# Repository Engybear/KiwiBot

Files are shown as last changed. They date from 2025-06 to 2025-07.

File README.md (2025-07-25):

# KiwiBot
<div align = "center"> 
  
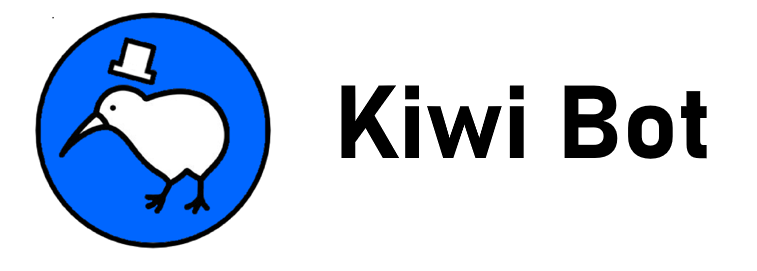
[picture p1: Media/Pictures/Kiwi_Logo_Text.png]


</div>

<!-- TOC -->
* [KiwiBot](#kiwibot)
  * [Inspiration, Purpose and Goals](#inspiration-purpose-and-goals)
  * [What It Does / Overview](#what-it-does--overview)
  * [File Organization / How It's Made](#file-organization--how-its-made)
  * [Challenges Faced](#challenges-faced)
  * [Accomplishments To Be Proud Of](#accomplishments-to-be-proud-of)
  * [Next Steps](#next-steps)

## Inspiration, Purpose and Goals
The public Ontario High School Curriculum only offers 6 courses regarding Computer Engineering and 0 courses regarding Electrical Engineering. Additionally schools are NOT required to facilitate this very limited selection of courses (only 9 out of the 26 schools in the Dufferin Peel Cathloic District offer a Computer Technology course). On interviewing high school teachers, many were frustrated that students say they want to be in STEM but don't know anything about it.

This project's motivation is to bridge the gap between classroom concepts and a physical, engaging and interactive module with the goal of sparking an interest in high schoolers to pursue engineering at the high school level.

The primary design goals of this project were to do what other hobby robots didn't, to invoke a sense of technically prowress. Research identified omni-directional movement, a single-handed control system, and real-time feedback to be areas of focus.

## What It Does / Overview
KiwiBot is a small-sized (10x10x16'') robot, capable of omni-directional movement on a planar surface using a KiwiDrive drive system, controlled by a gyroscopic sensor on a one-size-fits-all wearable glove and makes use of LED states and an accompanying computer program to provide optional feedback to the user.

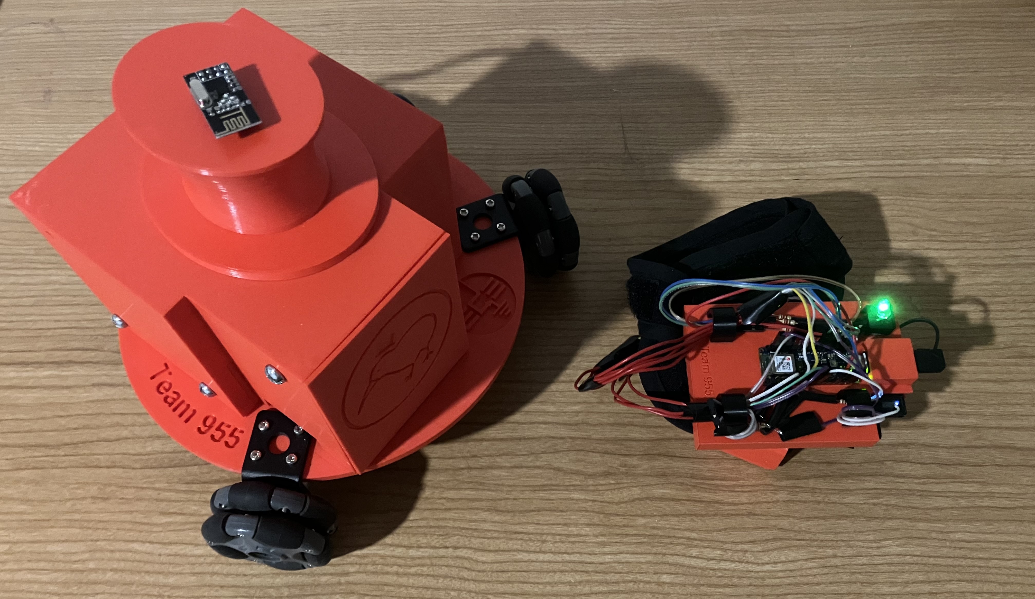
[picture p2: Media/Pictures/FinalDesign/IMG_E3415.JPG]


### Design Breakdown

Here you can see an overview of the design with inputs/outputs designated as circles at the bottom, primarily virtual processes in green, robot encapsulated structures in pink, handheld/glove controller encapsulated structures in blue, and the accompanied UI display structure in orange.

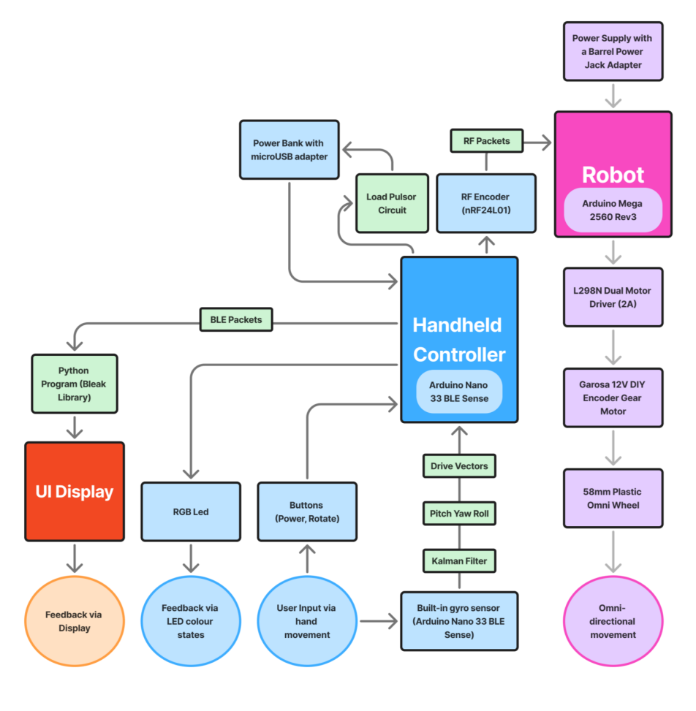
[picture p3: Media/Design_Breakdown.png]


- Refer to Media/Pictures and Videos to see KiwiBot in action

## File Organization / How It's Made

Refer to User Guide for setup and usage information

Refer to Construction Guide for system design information

Refer to arduino_sketches for the logic of the robot, the glove controller and tuning which are written in `C++`

Refer to scripts for supportive visuals that can be run on a computer which are written in `Python`

Refer to CAD_Files for CAD design and 3D printing files created in `Fusion360`

## Challenges Faced
The greatest challenge of this project was getting accurate tilt controls that felt good and intuitive. Of the ~25 people that used the design, it’s clear that for some it comes very easily,
while for others it’s hard to understand. During the early phases of construction, one of the major choices being made was to use either an MPU6050 or an MCU with built-in IMUs
like the Arduino Nano 33 BLE Sense Rev2 (BMI270 + BMM150). Due to a desire to simplify the hardware on the Controller as much as possible along with budget constraints, the Arduino Board with built-in sensors would be selected. It should be noted that both IMUs are able to achieve a IMU measurement range of +/- 4 Gs on the accelerometer and +/- 2000 deg/s on the
gyroscope, but the Arduino also has the BMM150 to make it a 9-axis sensor. Another consideration going into choosing the Arduino is that with an internal measurement unit built-in, sampling rate is automatically handled and overhead to prompt the sensors is minimized, whereas with an external measurement unit, communication would have to be over a serial bus and potentially susceptible to noise from other hardware on the controller. 

It should also be noted after much testing, that the magnetometer (BMM150) is highly unreliable and susceptible to noise in the environment, hence its influence in the Kalman Filter design was heavily reduced to be a simple error tracking term for the gyroscopic sensor’s yaw predictions. Over the course of the project several different filters would be tested to get better results. The process can be seen in the gyro_tuning.ino file, which contains the functions used to tune the gyroscopic and magnetometer sensors, as well as manually analyzing the predictions of independent sensors alone, complementary filters, and Madgwick filters. To see these, simply connect the Arduino Nano to a computer, uncomment a desired function in the main loop of the program in Arduino IDE and upload the sketch. The Kalman filter would however be selected and implementing in the gyro_main_ble.ino file because it was highly tunable to the design, leading to the best results given the condition that the Controller is not turned upside down as a result of using Euler angles over quaternions. It is a result of all these considerations and a LOT of testing and tuning for error margins that this challenge was conquered.

## Accomplishments To Be Proud Of
This project has two major accomplistments I would personally like to highlight:

I would firstly like to shoutout two private high schools, Sherwood Heights School and Kings Christian Collegiate, for allowing me to present the design in a live environment to high school students who wanted to learn more about engineering. Seeing a project through to a point were a target audience can use the design and I can collect feedback for further adjustments and improvements is always a pleasure and making an impact on worth celebrating. I should also note that on follow-up conversations with my contacts at these schools, I would learn that students would continue to discuss the event for a few days after it occured.

Secondly I'd like to shoutout my supervising professor, Belinda Wang, who nominated the project for a distinction in recognizing the effort that was put in and the results it would achieve. Additionally, the professor, among the other schools who were also interested in acquiring the project, was so impressed she would acquire KiwiBot for $591.99 to use in future demonstrations in highlighting the engineering design process.



## Next Steps
1. Single-handed tilt controls are unique and technically impressive to students, as well as
covers up the floaty control and motor drift during runtime. That said, there are ultimately
better methods of control. It was determined about halfway through the project that a
controller with 2 analog potentiometer joysticks (one to control orientation and one to
control direction of movement; or simply just one for the latter) rather than a glove would
be easier and snappier to control, assuming PID control is implemented to remove motor
drift. It is entirely possible to implement a controller that does both joystick and tilt
control and can swap between those methods of control, even while maintaining the
wearable glove concept.
2. One of the major recommendations for taking this project further is reducing costs to turn
it into a workshop kit. A drastic way to do this would be to cut out the Robot entirely.
With the hardware of the Controller alone, the project would consist of the Arduino Nano
33 BLE Sense Rev2, two push buttons, an RGB Led, and the power bank. However, even
such a large power bank used in the project is not needed and can be swapped out for AA
batteries instead, given the low power nature of the Controller. This would reduce costs
approximately to $80 per kit.
3. In tandem with Recommendation 2, without a physical Robot the simulation software
should be heavily advanced. It is possible to let students CAD out their own KiwiDrive
Robot or use a base template Robot, for which they can port into a 3D software
simulation and control the Robot through a digital landscape with the Controller. Once
they have done a software simulation test, they could try their controller out on the real
thing, with one shared physical Robot, that we’ve already made. This would be a major
undertaking potentially worth another Capstone Project.
4. Another method of reducing costs would be to not use Arduino boards that come with a
lot of extra bloat hardware but rather have a person who can design custom PCBs with
select chips, which was originally intended at the start of this project. Currently ~25% of
the project costs are from the Arduino boards. This would also help reduce space these
components require.
5. The wiring of the Controller is exposed and very vulnerable to weather conditions.
Although it wasn’t in the scope of this project, it was initially desired and is
recommended that the hardware for the Controller be contained within a protective
casing.
6. Occasionally PWM/DIR wires connecting to the Arduino Mega 2560 (on the second
layer) come loose from the L298Ns (on the base layer). Find a fix for this; currently using
electrical tape as a stand-in.
7. Fix sticky button on Controller.

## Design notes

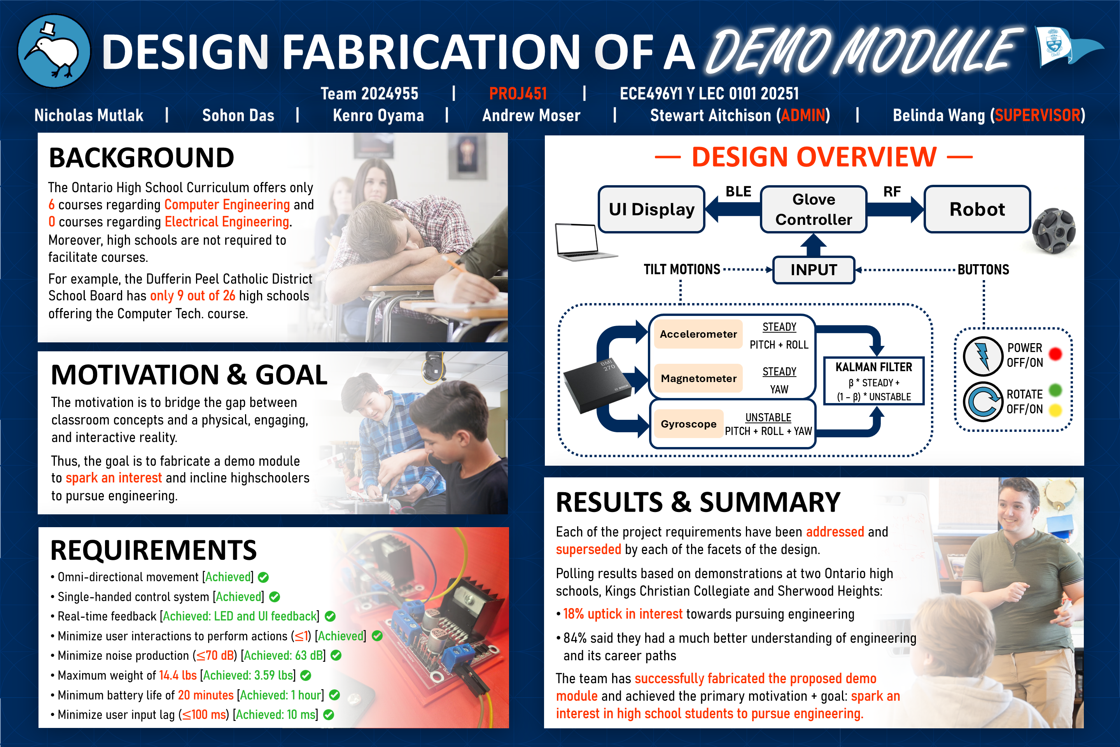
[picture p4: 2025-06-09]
Capstone_Poster.PNG

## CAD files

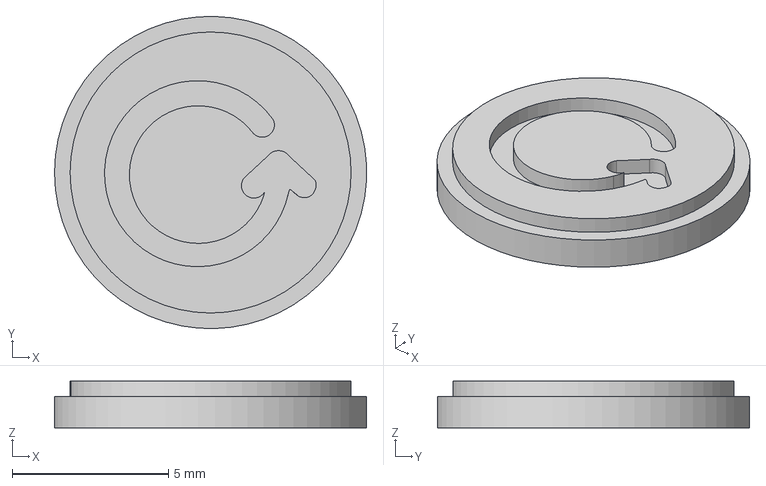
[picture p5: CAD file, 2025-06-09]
CAD_Files/glove/G2_KeyCap_Rotate.step
9.99 x 10.00 x 1.50 mm

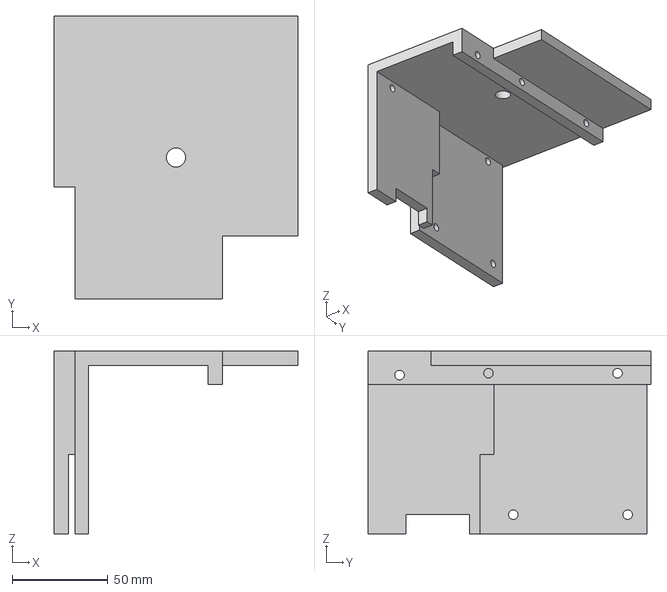
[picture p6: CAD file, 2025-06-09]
CAD_Files/robot/R2_Roof.step
127.6 x 148.0 x 95.5 mm

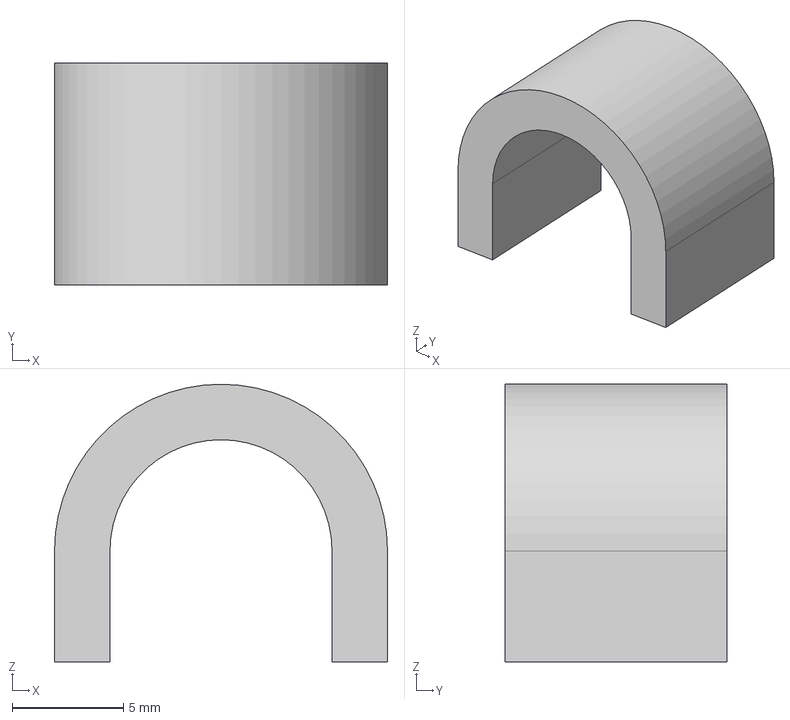
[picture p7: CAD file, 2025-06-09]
CAD_Files/glove/G2_Battery_WireHook.step
15.0 x 10.0 x 12.5 mm

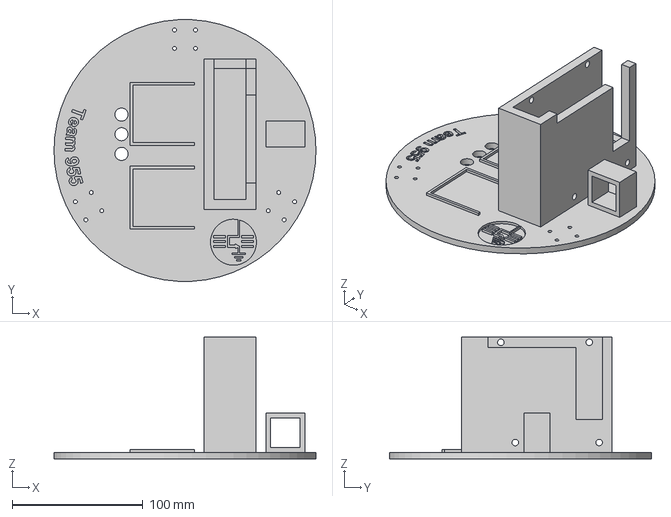
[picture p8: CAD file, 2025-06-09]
CAD_Files/robot/R2_Base.step
200.0 x 199.7 x 93.0 mm

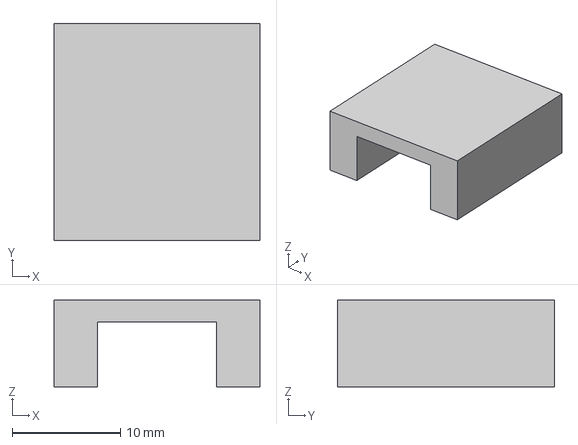
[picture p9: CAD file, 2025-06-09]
CAD_Files/glove/G2_Battery_Hook.step
19.0 x 20.0 x 8.00 mm

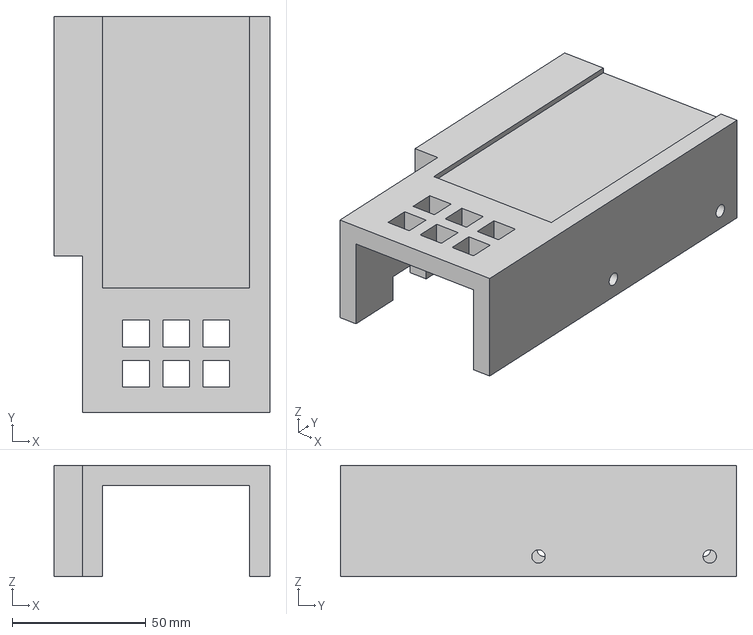
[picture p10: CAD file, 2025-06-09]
CAD_Files/robot/R2_ArduinoBase.step
80.6 x 148.0 x 41.5 mm

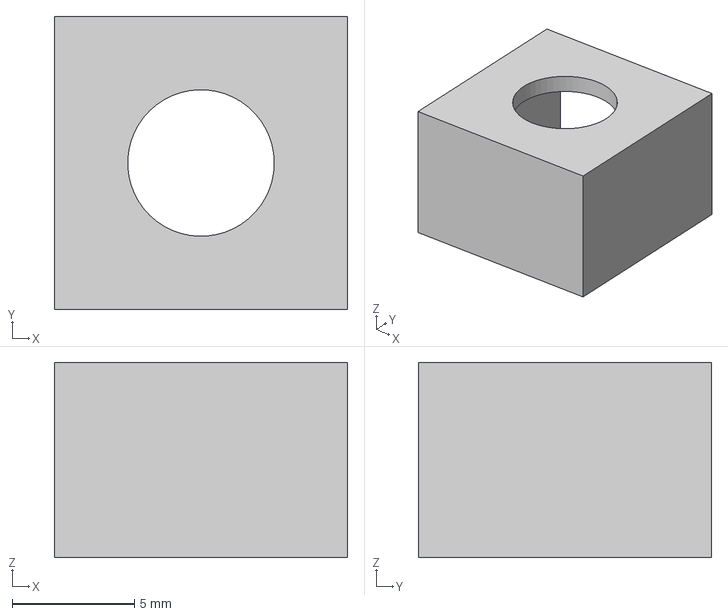
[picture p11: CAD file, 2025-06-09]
CAD_Files/glove/G2_RGB_Hook.step
12.0 x 12.0 x 8.00 mm

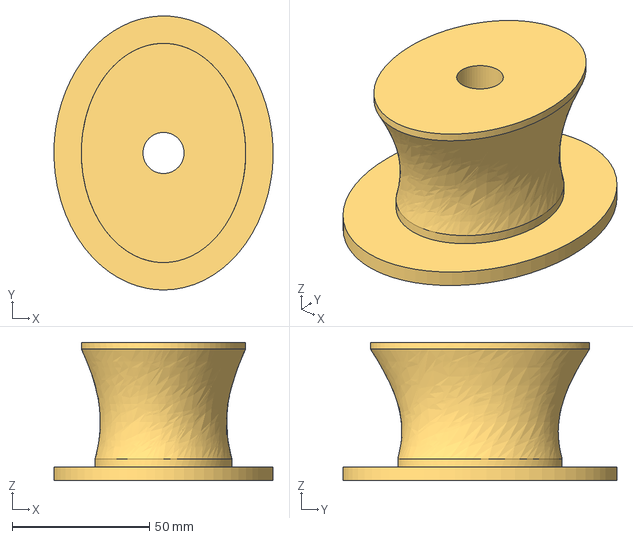
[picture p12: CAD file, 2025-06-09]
CAD_Files/robot/R2_Hat.step
79.9 x 100.0 x 50.5 mm

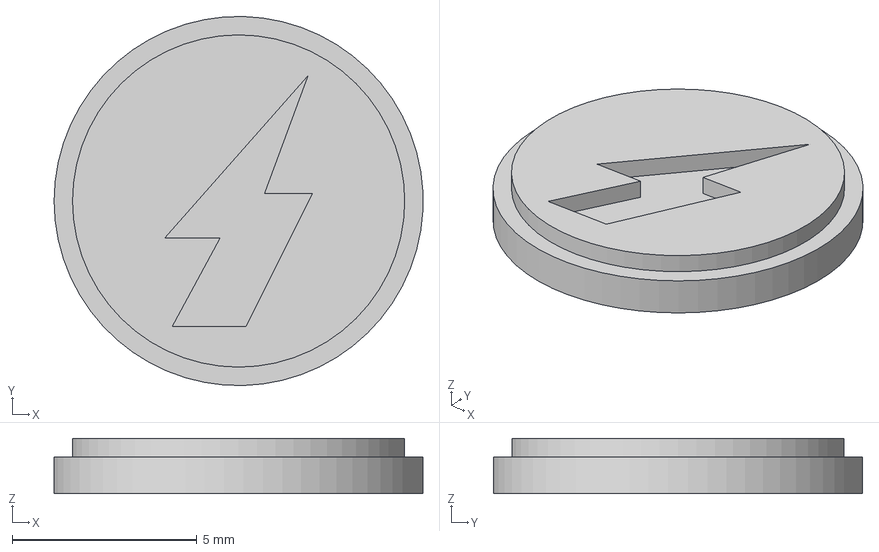
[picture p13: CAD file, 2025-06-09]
CAD_Files/glove/G2_KeyCap_Power.step
9.99 x 10.00 x 1.50 mm

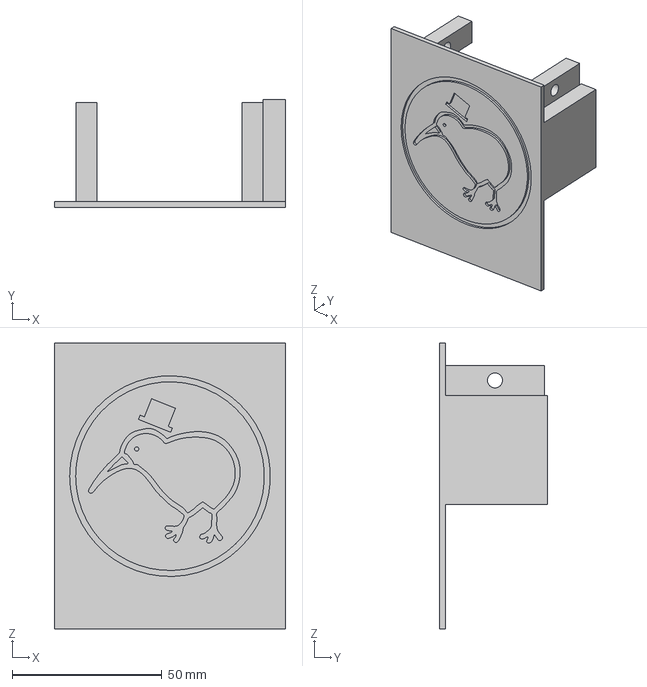
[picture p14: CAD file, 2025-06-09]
CAD_Files/robot/R2_FrontPlate.step
77.2 x 36.0 x 95.5 mm

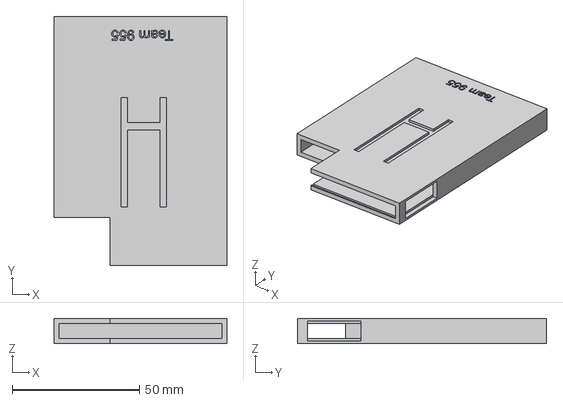
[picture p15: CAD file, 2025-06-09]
CAD_Files/glove/G2_Battery_Case.step
68.0 x 98.0 x 10.0 mm

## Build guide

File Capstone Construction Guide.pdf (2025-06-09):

## Capstone Project: KiwiBot Construction Guide

Nicholas Mutlak

University of Toronto

April 10th, 2025

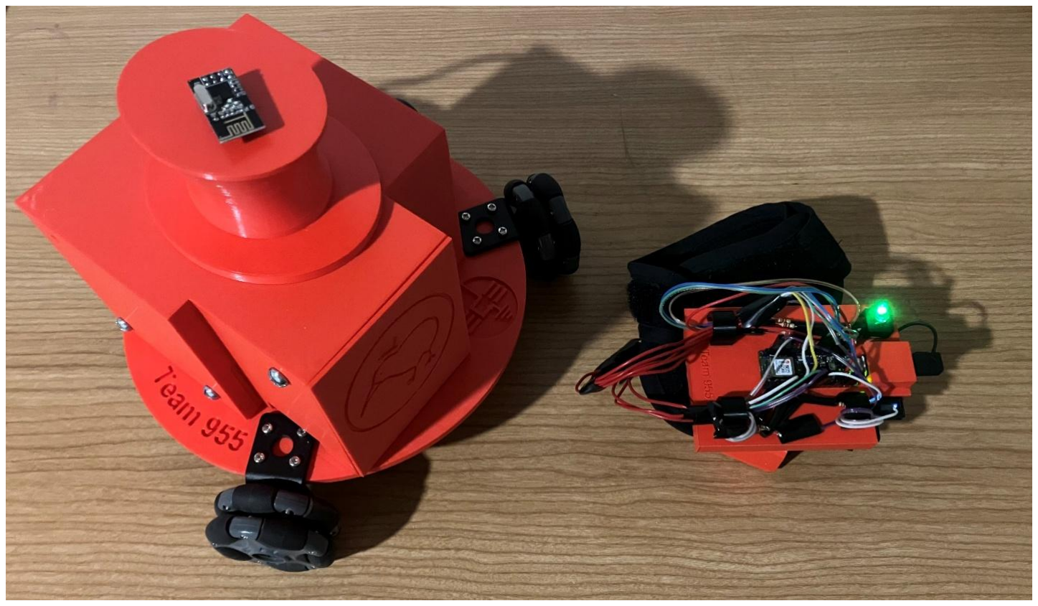
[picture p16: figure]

Introduction

During the academic year of 2024-2025, a robot that will be referred to as ‘KiwiBot’ was designed, built, and programmed. The purpose of this robot was to spark interest in engineering for high school students through a technically impressive design and a hands-on interactive controller, that would do what most other hobby robots don’t. This guide entails brief details about the robot’s design process, construction, and programming. For more detailed information refer to the project’s Final Report. For control and troubleshooting refer to the project’s User Guide.

Parts List

Part | Qty | Link
Laptop | 1 | Borrowed
Arduino Mega 2560 Rev3 | 1 | https://www.canadarobotix.com/collections/featured-1/products/266 (https://www.canadarobotix.com/collections/featured-1/products/266)
L298N Motor Drivers | 1 | https://www.amazon.ca/PChero-2Packs-Controller-Stepper-Arduino/dp/B07C4B3DL4/ (https://www.amazon.ca/PChero-2Packs-Controller-Stepper-Arduino/dp/B07C4B3DL4/)
58mm Plastic Omni Wheels | 3 | https://ca.robotshop.com/products/58mm-plastic-omni-wheel-compatible-servos-lego-mindstorms-nxt (https://ca.robotshop.com/products/58mm-plastic-omni-wheel-compatible-servos-lego-mindstorms-nxt)
Garosa 12V DIY Encoder Gear Motor | 3 | https://www.amazon.ca/dp/B07WRYYG4G
USB A/B Connector | 1 | Personal Donation
Talentcell Rechargeable 12V 3000mAh Lithium ion Battery Pack | 1 | https://www.amazon.ca/dp/B01M7Z9Z1N
DC Adapter Female Barrel Power Jack | 1 | https://www.amazon.ca/dp/B0D3VDG88R
Arduino Nano 33 BLE Sense Rev2 | 1 | https://www.canadarobotix.com/products/3031
TNTOR Power Bank 5V 2500mAH | 1 | https://www.amazon.ca/dp/B0CJFMNKBV
USBC / MicroUSB Adapter | 1 | https://www.amazon.ca/Adapter-BabyElf-Convert-Connector-Compatible/dp/B087WKS9NZ/
Push Buttons | 2 | MyFab
nRF24L01 RF Module | 2 | https://www.canadarobotix.com/products/2437
Assorted Wires | X | MyFab
Assorted Machine Screws / Bolts | X | Personal Donation / RONA

The chassis on which all these parts are mounted, as well as the hex shafts for the wheels were 3D printed by a Ender Pro 3 v2 in 5 main sections for the robot and 3 main sections for the controller. The robot’s sections are connected together in place through M10 machine screws and nuts. The controller’s battery case is standalone, while the button case is two distinct pieces connected together by M4 machine screws and bolts. Superglue was used for different mounts.

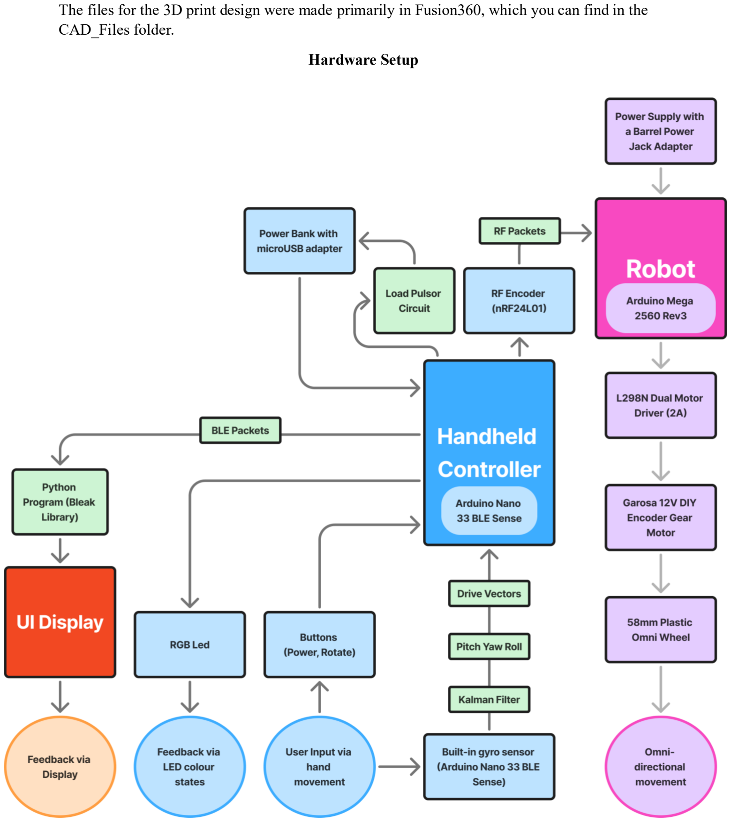
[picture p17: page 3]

The files for the 3D print design were made primarily in Fusion360, which you can find in the CAD_Files folder.

Hardware Setup

The design is meant to take tilt controls measured from the controller’s Arduino Nano 33 BLE Sense Rev2 and convert them to control signals of X,Y (planar) and W (rotational) velocities. The buttons on the robot control when these velocities are allowed to be non-zero or if they get scaled up or down. There are 3 main states which are displayed by the LED. The Power button is primary, displaying Red when off and the zero-ing out the velocities regardless of tilt. When pressed the controller will either be in the Green or Yellow state (green being only planar movement and yellow allowing for rotational movement). The states can be swapped with the secondary Rotate button. All this information is packaged into RF and BLE packets, to be sent to the robot and a computer respectively to control to the robot as well as show the controls in real time on a display.

The communication range on these devices is reliable to at minimum 80ft and in theory can reach a max range of 900ft if there are no obstructions.

Both batteries of the controller and robot are rechargeable. Theoretical runtime of robot on max motor output is 2.5 hours with tested runtime being at minimum 1 hour of use. Theoretical runtime of controller is 24 hours with tested runtime being at minimum 1 hour of use. Recharging the robot usually takes approximately an hour and the glove approximately under 30 minutes depending on how much the devices are drained.

The robot’s Arduino Mega 2560 Rev3 has the pinout capacity to support PID control with the Garosa motor’s encoders. It was deemed in the scope of the project and the floaty-feeling control of the glove controller that it would not be necessary. Additionally, the robot’s MCU is also capable of supporting more peripherals such as a 4th motor, collision sensors or other communication modules if desired.

The TNTOR Power Bank for the controller has an auto shut off feature, as it’s original intention is to charge phones and the current draw of all the controller’s components is not large enough to register above its detector’s threshold. The load pulser circuit was then designed, with a simple resistor network of a ~50 Ohm load wired the 5V USB line to draw 100mA of current from the battery. Doing this through the Arduino Nano board itself is a risk as its not designed to draw that much current at a constant rate due to risks of overheating, and as such a transistor is used to pulse the circuit only every 30 seconds, saving battery life as well as providing protection to the MCU.

Programming

Arduino IDE was used to program in C++ and upload sketches stored as .ino files to both of the Arduino boards. The Arduino Nano 33 BLE Sense Rev2 has been uploaded the glove_main_ble.ino sketch, while Arduin Mega 2560 Rev3 has been uploaded the robot_main.ino sketch. To upload a new sketch to any of the boards, connect a USB cable between the board and your computer, and upload via Arduino IDE.

BMI270 / BMM150 IMU Sensors

The greatest challenge of this project was getting accurate tilt controls that felt good and intuitive. Of the ~25 people that used the design, it’s clear that for some it comes very easily, while for others it’s hard to understand. That aside, during the early phases of construction, one of the major choices being made was to use either an MPU6050 or an MCU with built-in IMUs like the Arduino Nano 33 BLE Sense Rev2 (BMI270 + BMM150). Due to a desire to simplify the hardware on the Controller as much as possible along with budget constraints, the team would select the Arduino Board with built-in sensors. It should be noted that both IMUs are able to achieve a IMU measurement range of +/- 4 Gs on the accelerometer and +/- 2000 deg/s on the gyroscope, but the Arduino also has the BMM150 to make it a 9-axis sensor. A more comparable external IMU would be the MPU9250. Another consideration going into choosing the Arduino is that with an internal measurement unit built-in, sampling rate is automatically handled and overhead to prompt the sensors is minimized, whereas with an external measurement unit, communication would have to be over a serial bus and potentially susceptible to noise from other hardware on the controller.

It should also be noted after much testing, that the magnetometer (BMM150) is highly unreliable and susceptible to noise in the environment, hence its influence in the Kalman Filter design was heavily reduced to be a simple error tracking term for the gyroscopic sensor’s yaw predictions.

Over the course of the project several different filters would be tested to get better results. The process can be seen in the gyro_tuning.ino file, which contains the functions used to tune the gyroscopic and magnetometer sensors, as well as manually analyzing the predictions of independent sensors alone, complementary filters, and Madgwick filters. To see these, simply connect the Arduino Nano to a computer, uncomment a desired function in the main loop of the program in Arduino IDE and upload the sketch. The Kalman filter would however be selected and implementing in the gyro_main_ble.ino file because it was highly tunable to the design, leading to the best results given the condition that the Controller is not turned upside down as a result of using Euler angles over quaternions.

Python UI App

This is a rudimentary matplotlib application, initially deemed infeasible, as I’m personally inexperienced with proper app design and working with BLE on Windows. This program using the Bleak python library to connect to the advertising service that the Controller sends out to receive information and visually displays how the Robot handles that information with the drive vectors shown on screen. There are two threads that run asynchronously; one updates a list of shared global variables using the Bleak library, while the other updates the UI based on these variables. It was made as an aid to first time users that struggled to understand how to control the robot, however it’s effectiveness in doing so is questionable, as a user would have to focus their attention between the Robot’s movements, their hand movements, as well as the UI display.

Recommendations for the Future

1. Single-handed tilt controls are unique and technically impressive to students, as well as covers up the floaty control and motor drift during runtime. That said, there are ultimately better methods of control. It was determined about halfway through the project that a controller with 2 analog potentiometer joysticks (one to control orientation and one to control direction of movement; or simply just one for the latter) rather than a glove would be easier and snappier to control, assuming PID control is implemented to remove motor drift. It is entirely possible to implement a controller that does both joystick and tilt control and can swap between those methods of control, even while maintaining the wearable glove concept.
2. One of the major recommendations for taking this project further is reducing costs to turn it into a workshop kit. A drastic way to do this would be to cut out the Robot entirely. With the hardware of the Controller alone, the project would consist of the Arduino Nano 33 BLE Sense Rev2, two push buttons, an RGB Led, and the power bank. However, even such a large power bank used in the project is not needed and can be swapped out for AA batteries instead, given the low power nature of the Controller. This would reduce costs approximately to $80 per kit.
3. In tandem with Recommendation 2, without a physical Robot the simulation software should be heavily advanced. It is possible to let students CAD out their own KiwiDrive Robot or use a base template Robot, for which they can port into a 3D software simulation and control the Robot through a digital landscape with the Controller. Once they have done a software simulation test, they could try their controller out on the real thing, with one shared physical Robot, that we’ve already made. This would be a major undertaking potentially worth another Capstone Project.
4. Another method of reducing costs would be to not use Arduino boards that come with a lot of extra bloat hardware but rather have a person who can design custom PCBs with select chips, which was originally intended at the start of this project. Currently ~25% of the project costs are from the Arduino boards. This would also help reduce space these components require.
5. The wiring of the Controller is exposed and very vulnerable to weather conditions. Although it wasn’t in the scope of this project, it was initially desired and is recommended that the hardware for the Controller be contained within a protective casing.
6. Occasionally PWM/DIR wires connecting to the Arduino Mega 2560 (on the second layer) come loose from the L298Ns (on the base layer). Find a fix for this; currently using electrical tape as a stand-in.
7. Fix sticky buttons on Controller.

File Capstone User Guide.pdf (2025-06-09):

## Capstone Project: KiwiBot User Guide

Nicholas Mutlak

University of Toronto

April 10th, 2025


Introduction

During the academic year of 2024-2025, a robot that will be referred to as ‘KiwiBot’ was designed, built, and programmed. The purpose of this robot was to spark interest in engineering for high school students through a technically impressive design and a hands-on interactive controller, that would do what most other hobby robots don’t. This guide entails how to use the robot. For more detailed information refer to the project’s Final Report. For an overview of project’s construction details refer to the project’s Construction Guide.

Step-by-Step Setup Guide for New Users

1. Plug in Robot’s USB and Barrel Jack power cables and turn on the power bank (Refer to Figure 1). The Robot’s MCU (Arduino Mega 2560 Rev3 on second layer) should be preloaded with robot_main.ino sketch.

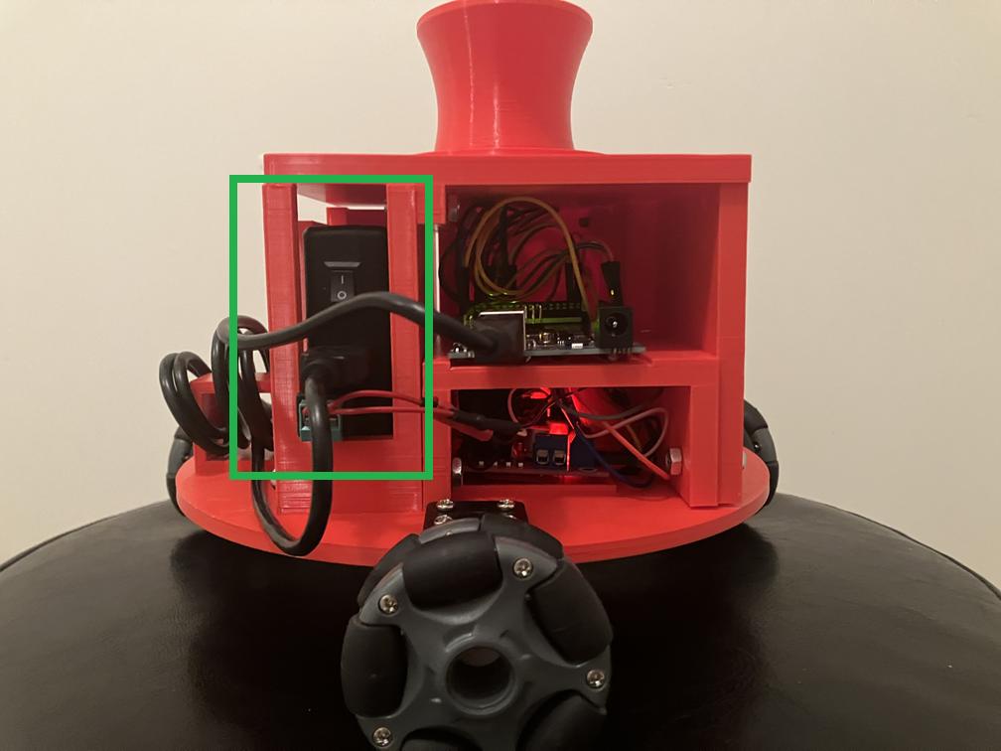
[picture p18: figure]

Figure 1: Power Bank Input Locations

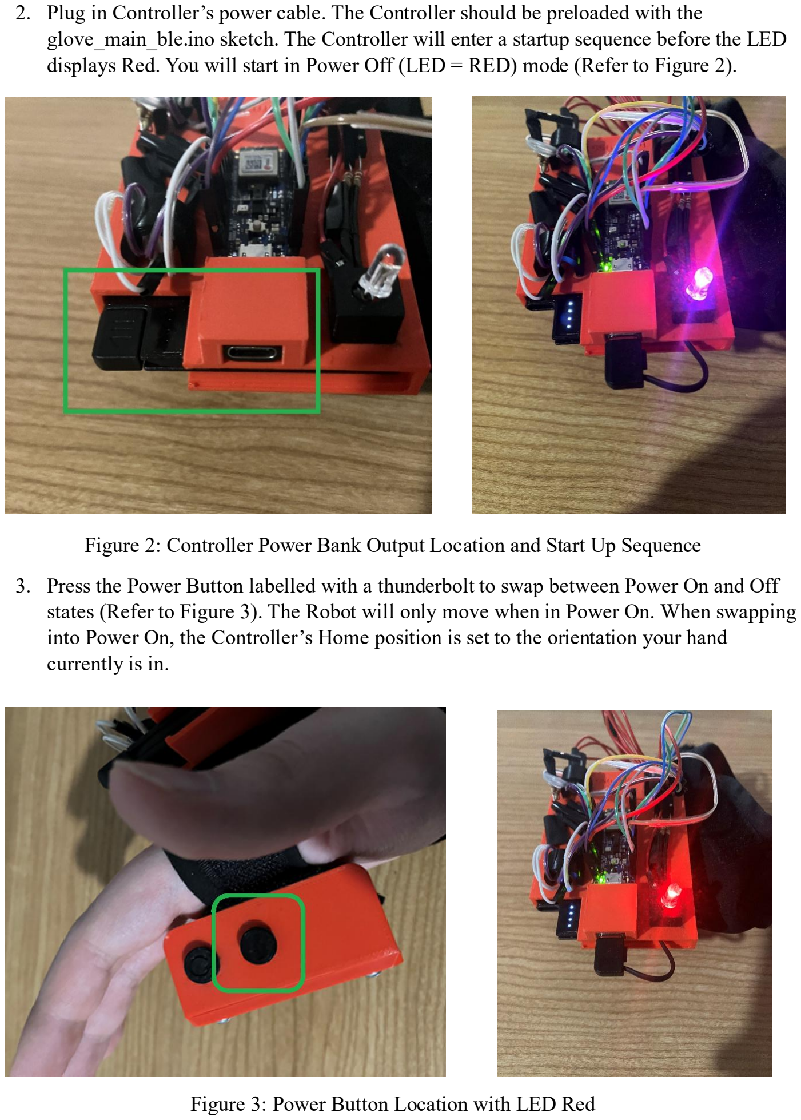
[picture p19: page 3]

2. Plug in Controller’s power cable. The Controller should be preloaded with the glove_main_ble.ino sketch. The Controller will enter a startup sequence before the LED displays Red. You will start in Power Off (LED = RED) mode (Refer to Figure 2).

Figure 2: Controller Power Bank Output Location and Start Up Sequence

3. Press the Power Button labelled with a thunderbolt to swap between Power On and Off states (Refer to Figure 3). The Robot will only move when in Power On. When swapping into Power On, the Controller’s Home position is set to the orientation your hand currently is in.

Figure 3: Power Button Location with LED Red

4. Press the Rotate Button labelled with an arrow to swap between Rotate Off and On states (Refer to Figure 4). In Rotate Off (LED = GREEN), only planar movement will be allowed in X and Y. In Rotate On (LED = YELLOW), both planar and rotation movement will be allowed in X, Y, and W.

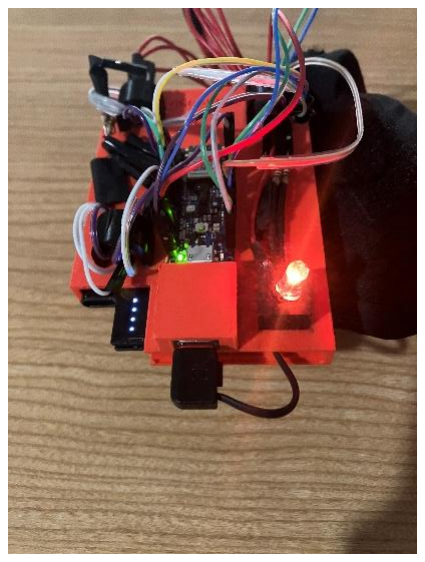
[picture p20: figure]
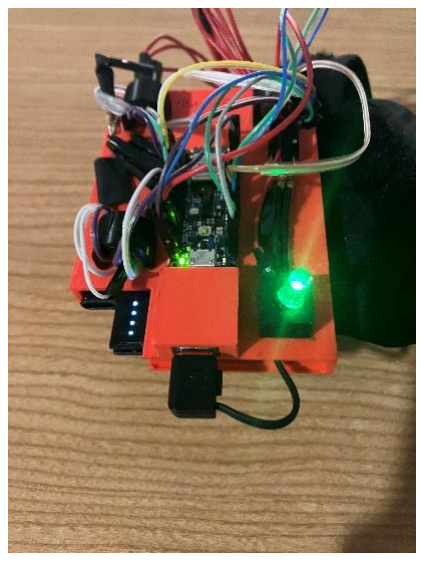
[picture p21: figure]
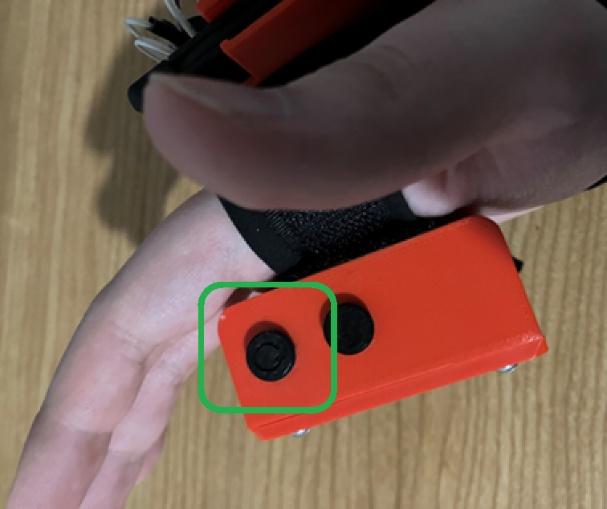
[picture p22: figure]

Figure 4: Rotate Button Location with LED Green and Yellow

5. To move the Robot, all tilt motions of the hand are confined between 45 degrees of the Home position. It is HIGHLY recommended to not tilt your hand 90 degrees or upside down, as this makes it very difficult for the IMU to get accurate pitch, roll and yaw measurements. To move the Robot left, ease your hand in the roll direction left. To move the Robot forward, ease your hand down in the pitch direction. To rotate the Robot, turn your hand like turning a knob (Refer to Figure 5). It is HIGHLY recommended to have the glove comfortably tight to reduce wobble during tilt motions and to take movement slowly.

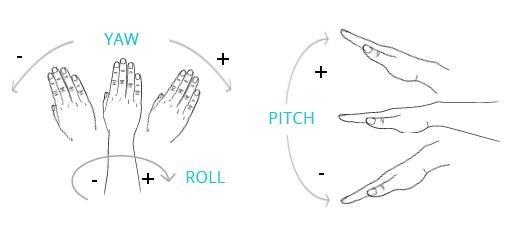
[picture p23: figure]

Figure 5: Visual Mock-Up of Pitch, Roll and Yaw of Hand from Home Position

6. (Optional) Run the accompanying BLE python script (sim_ble.py) when the Controller is on. The program should be compatible with any device on Linux, MacOS or Windows, provided the device can support BLE connections and has both python and the python “Bleak” library installed (type pip install bleak in a terminal to do so). When the program is running, enter 0 into the terminal to exit. While running it will display the information the Controller is sending to the Robot in real time (refer to Figure 6).

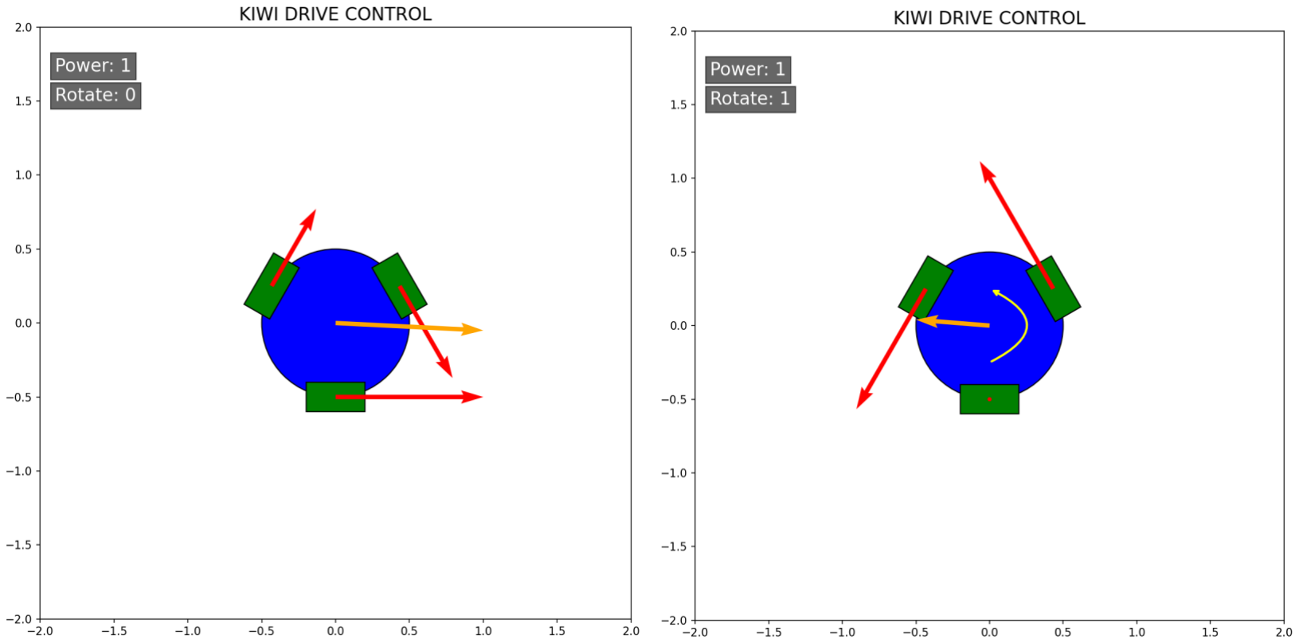
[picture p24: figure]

Figure 6: Two Examples of Complementary UI Program During Runtime

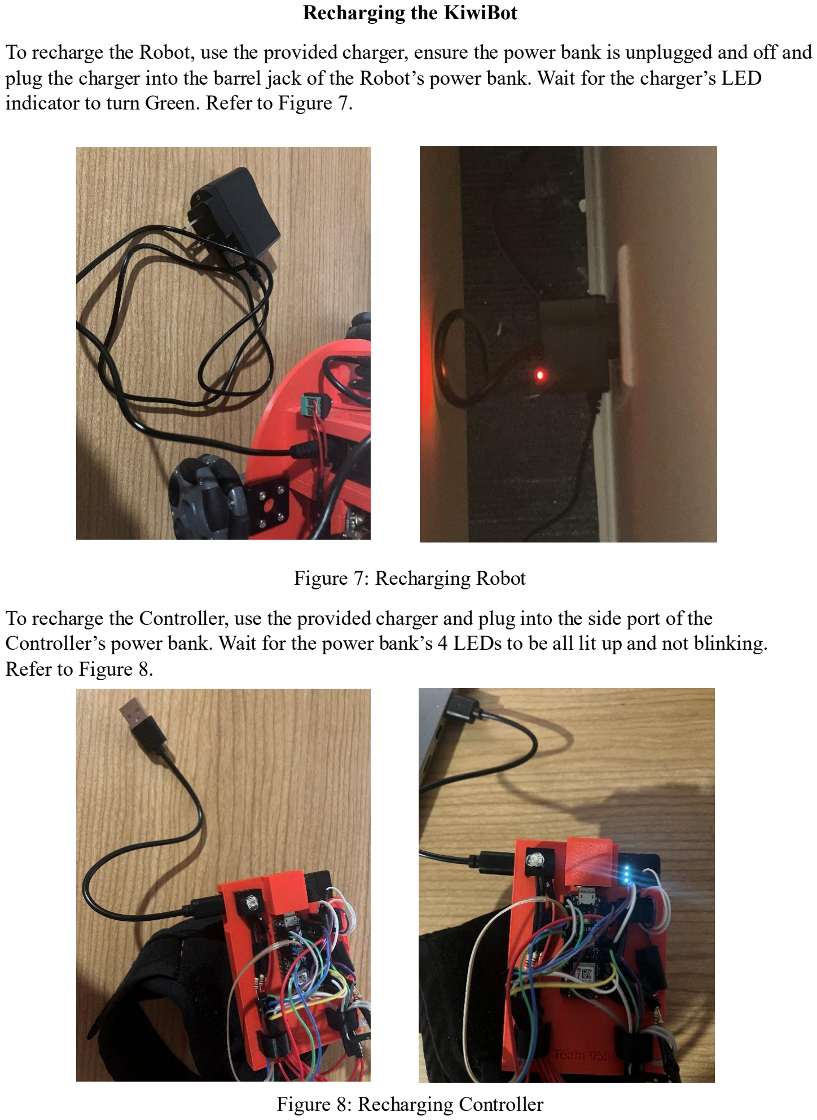
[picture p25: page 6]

Recharging the KiwiBot

To recharge the Robot, use the provided charger, ensure the power bank is unplugged and off and plug the charger into the barrel jack of the Robot’s power bank. Wait for the charger’s LED indicator to turn Green. Refer to Figure 7.

Figure 7: Recharging Robot

To recharge the Controller, use the provided charger and plug into the side port of the Controller’s power bank. Wait for the power bank’s 4 LEDs to be all lit up and not blinking. Refer to Figure 8.

Figure 8: Recharging Controller

Known Issues and Troubleshooting Tips

- DO NOT leave the Robot unattended to charge over a long period of time. Although the battery likely has built-in protections, overcharging the Robot can damage the battery.
- DO NOT expose the Robot or any components to water / weather conditions.
- DO NOT hold the Robot on its side. The D-shaft adapters connecting the omni-wheels to the motor shafts are 3D printed and can allow the omni-wheels to slide off. During standard operation this is not an issue, although superglue can be recommended as more permanent solution.
- DO be gentle with the devices during transport and operation. Measures were taken to bolster their sturdiness and wire connections, however they are not infallible.
- The Robot will drift imperfectly in X, Y planar movement. You can account for this rather easily with manual nature of adjusting tilt controls. An alternative fix to this, would be to implement PID control using the encoders built into the motors. The encoder wires are currently unused and taped to the bottom of the Robot.
- If one of the wheels isn’t working (stops rotating or rotates only in one direction) it’s likely because of a loose wire connection on the Arduino Mega 2560 on the second layer of the Robot. Electrical tape has been used to mitigate this issue, but the effectiveness of this solution is untested.
- Sometimes the buttons will stick or double press, often confusing first time users when they accidentally cycle between Power ON / OFF. This is an issue with the design involving supergluing the keycaps comparatively small push buttons. Potential fixes would involve using entirely different push buttons that can better accommodate a keycap.

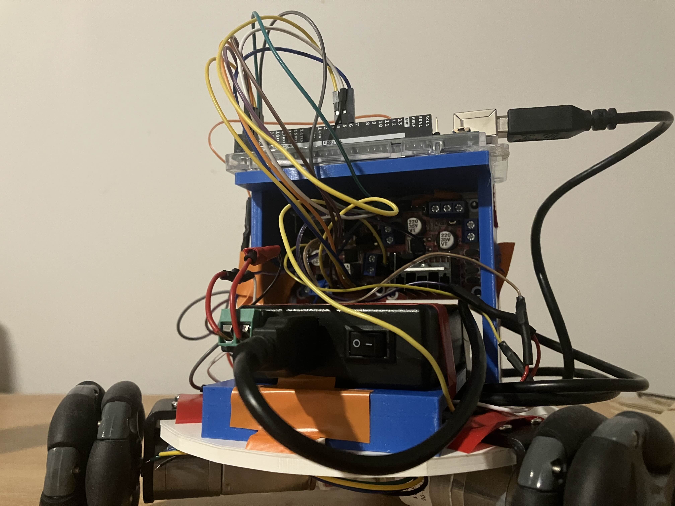
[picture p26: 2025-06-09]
Media/Pictures/Building/IMG_3171.jpg

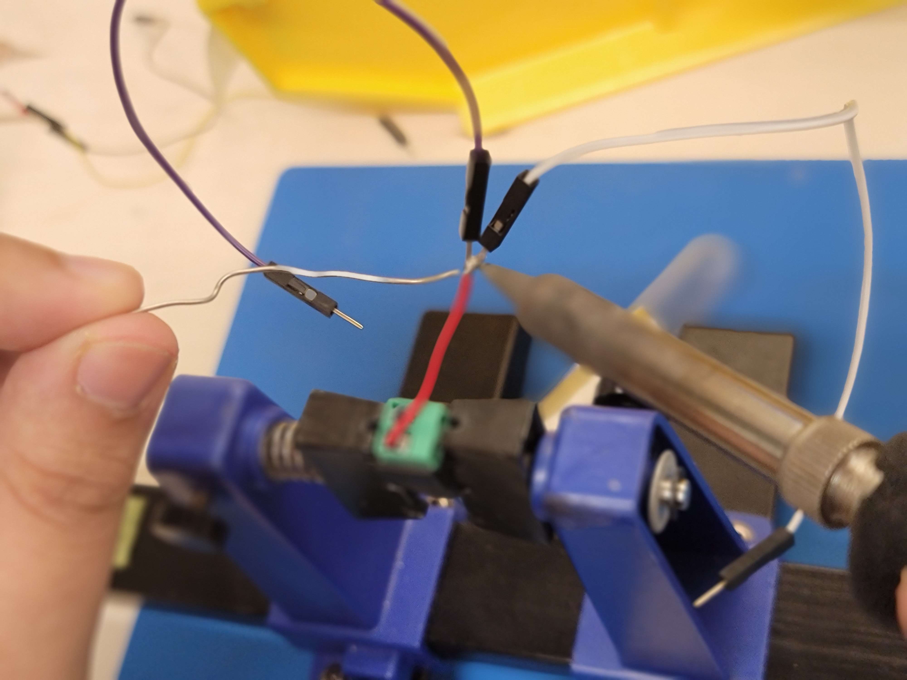
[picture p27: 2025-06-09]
Media/Pictures/Building/20241126_153629.jpg

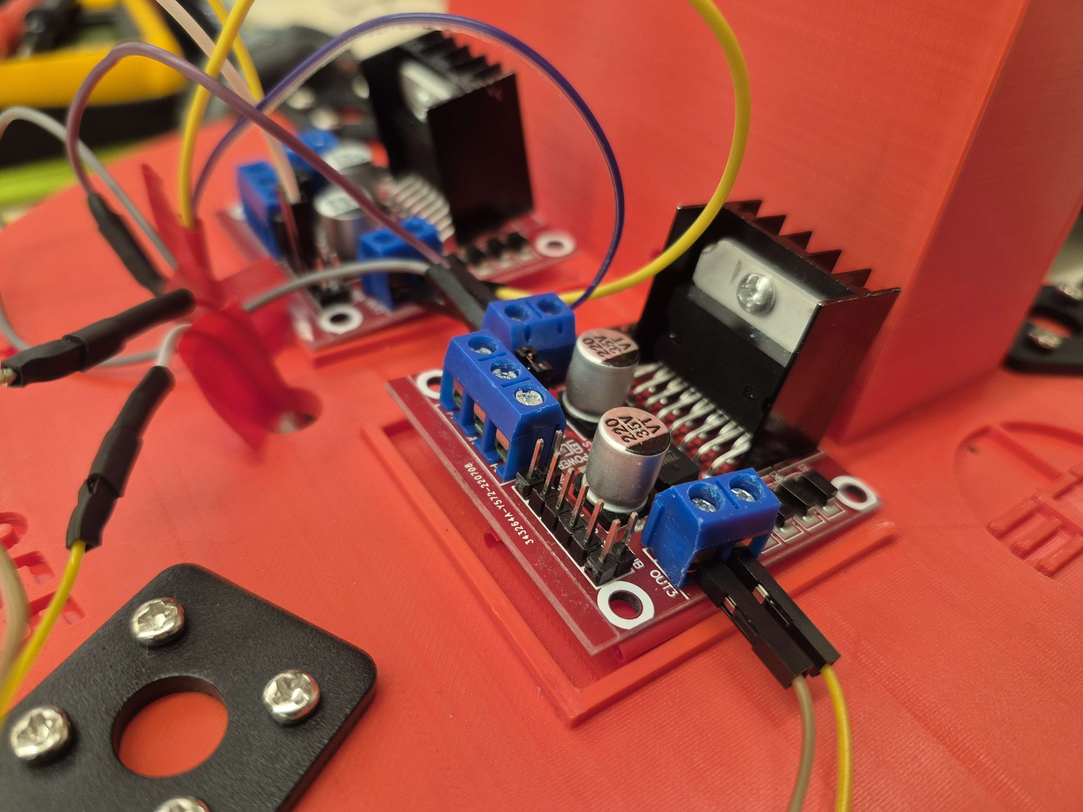
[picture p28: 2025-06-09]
Media/Pictures/Building/20250113_131736.jpg

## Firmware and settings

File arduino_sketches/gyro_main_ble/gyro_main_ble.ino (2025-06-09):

#include <SPI.h>
#include <nRF24L01.h>
#include <RF24.h>
#include <Arduino_BMI270_BMM150.h>
#include <ArduinoBLE.h>

// define pins for nRF24 modul
#define CE_PIN 2
#define CSN_PIN 3

// define pins for button inputs
#define power_button 5
#define rotate_button 4

// Define RGB LED pins (Common Anode)
const int greenPin = A0;  // green = brown on A0
const int redPin = A1;    // red = blue on A1
const int bluePin = A2;   // blue = green on A2
const int powerPin = D9;  // power to hold 3.3V HIGH value

// *ENUM MUST BE AT THE TOP OF THE FILE BEFORE STRUCTS / FUNCS
enum ledColour { // enumerated list of all RGB colours
  Red,
  Green,
  Blue,
  Yellow,
  Cyan,
  Magenta,
  White,
  Off
};
ledColour curColour = Magenta; // default colour state begins with Magenta on startup

// intialize radio for nRF24 module
RF24 radio(CE_PIN, CSN_PIN);
const byte address[6] = "00001";  // Address of the pipe

struct RF_Packet { // RF packet to process info received
  bool power; // Indicates whether motors should be active
  bool rotate; // Indicates whether rotation should be enabled
  float driveX; // X-direction movement
  float driveY; // Y-direction movement
  float driveW; // Rotational movement (W angular velocity)
}__attribute__((packed));
RF_Packet dataToSend = {true, true, 1.0, 1.5, 2.0}; // basic default values for testing

// flags that are updated on button presses
volatile bool calibrate_flag = false;
volatile bool power_buttonPressed = false;
volatile bool rotate_buttonPressed = false;
static unsigned long lastInterruptTime = 0; // used to ensure a single tap does not cause multiple interrupt calls

// Interrupt Service Routines for Buttons
void handlePowerPress(){
  unsigned long interruptTime = millis();

  if (interruptTime - lastInterruptTime > 100) {
    power_buttonPressed = !power_buttonPressed; // change state
    if(power_buttonPressed) calibrate_flag = true; // recalibrate Home Position of controller when power button is pressed on
    lastInterruptTime = interruptTime;
  }
}

void handleRotatePress() {
  unsigned long interruptTime = millis();
  
  // additional 0.3s delay requirement here due to sticky rotate button hardware
  if (interruptTime - lastInterruptTime > 300) { 
    rotate_buttonPressed = !rotate_buttonPressed;
    if (rotate_buttonPressed) calibrate_flag = true; // recalibrate Home Position of controller when rotate button is pressed on
  
    lastInterruptTime = interruptTime;
  }
}

// TILT MOTION CONTROL SETUP

float ax, ay, az;  // Accelerometer xyz values; Does not need calibration

float gx = 0, gy = 0, gz = 0;  // Gyro xyz values
float pitch_g = 0.0, roll_g = 0.0, yaw_g = 0.0; // global Gyro PRY values
float comp_yaw_g = 0.0; // additional complementary filter yaw value
float gx_offset = 0.00, gy_offset = 0.05, gz_offset = -0.24; // intended for calibration at high gyro_scale to help mitigate value drift
const int num_samples = 5000; // sample count used during Gryo calibration

float mx, my, mz;  // Magnetometer xyz values
// Magnetometer calibration values to help mitigate value drift
float mx_min =  -99.0, my_min =  -47.0, mz_min =  -46.0;
float mx_max = 27.0, my_max = 89.0, mz_max = 100.0;
bool calibrating = false;  // used during magnetometer calibration (Set to false after collecting enough data)

// store Home and Difference PRY values for tilt direction and magnitude
float base_roll = 0; 
float base_pitch = 0;
float base_yaw = 0;
float diff_roll = 0;
float diff_pitch = 0;
float diff_yaw = 0;

float now_time, prev_time, dt; // used to calculate dt on a scale of ms

// Kalman filter class setup
class Kalman {
public:
  Kalman(float Q_angle_in, float Q_bias_in, float R_measure_in) {
    Q_angle = Q_angle_in; // Process noise covariance (responsiveness)
    Q_bias = Q_bias_in;  // Bias covariance (adaption)
    R_measure = R_measure_in; // Measurement noise covariance (how much bias towards absolute estimator vs predictor)
    
    angle = 0.0;
    bias = 0.0;
    rate = 0.0;
    P[0][0] = 1.0; P[0][1] = 0.0; P[1][0] = 0.0; P[1][1] = 1.0;
  }

  float getAngle(float newAngle, float newRate, float dt) {
    // Predict
    rate = newRate - bias;
    angle += dt * rate;

    // Update covariance matrix
    P[0][0] += dt * (dt * P[1][1] - P[0][1] - P[1][0] + Q_angle);
    P[0][1] -= dt * P[1][1];
    P[1][0] -= dt * P[1][1];
    P[1][1] += Q_bias * dt;

    // Compute Kalman gain to model noise of system
    float S = P[0][0] + R_measure;
    float K[2];
    K[0] = P[0][0] / S;
    K[1] = P[1][0] / S;

    // Update estimate to a more accurate prediction
    float y = newAngle - angle;
    angle += K[0] * y;
    bias += K[1] * y;

    // Update covariance matrix
    float P00_temp = P[0][0];
    float P01_temp = P[0][1];
    P[0][0] -= K[0] * P00_temp;
    P[0][1] -= K[0] * P01_temp;
    P[1][0] -= K[1] * P00_temp;
    P[1][1] -= K[1] * P01_temp;

    return angle;
  }

private:
  float Q_angle, Q_bias, R_measure;
  float angle, bias, rate;
  float P[2][2];
};
Kalman kalmanPitch(0.01,0.003,0.02); // to be used with Accel and Gyro
Kalman kalmanRoll(0.01,0.003,0.02); // to be used with Accel and Gyro
Kalman kalmanYaw(0.01,0.003,0.001); // to be used wtih Mag and Gryo

// Load Pulser Gate Logic setup
const int pulse_gate = D6; // pin to control gate
bool gateState = LOW; // state of wheter the gate is open or closed
const int pulse_ON = 1000; // pulse battery with increased load for 1 second
const int pulse_OFF = 30000; // wait between pulses for 30 seconds
unsigned long interval = pulse_OFF; // time measurement variables
unsigned long pulse_prevTime = 0;

// sets RGB LED colour using PWM signals to control RGB value pins
// could be more advanced but only uses main enumerated colours for LED strength 
void set_ledColour(ledColour set_colour) {
  switch (set_colour) {
    case Red:
      analogWrite(redPin, 0);
      analogWrite(greenPin, 255);
      analogWrite(bluePin, 255);
      break;
    case Green:
      analogWrite(redPin, 255);
      analogWrite(greenPin, 0);
      analogWrite(bluePin, 255);
      break;
    case Blue:
      analogWrite(redPin, 255);
      analogWrite(greenPin, 255);
      analogWrite(bluePin, 0);
      break;
    case Yellow:
      analogWrite(redPin, 0);
      analogWrite(greenPin, 0);
      analogWrite(bluePin, 255);
      break;
    case Cyan:
      analogWrite(redPin, 255);
      analogWrite(greenPin, 0);
      analogWrite(bluePin, 0);
      break;
    case Magenta:
      analogWrite(redPin, 0);
      analogWrite(greenPin, 255);
      analogWrite(bluePin, 0);
      break;
    case White:
      analogWrite(redPin, 0);
      analogWrite(greenPin, 0);
      analogWrite(bluePin, 0);
      break;
    case Off:
      analogWrite(redPin, 255);
      analogWrite(greenPin, 255);
      analogWrite(bluePin, 255);
      break;
  }
}

// BLE setup
// findable advertising service and characteristic ID for data
const char *deviceServiceUUID = "891763a1-0d7f-48f1-b9fc-e403014730a1";
const char *deviceServicePacketCharUUID = "891763a3-0d7f-48f1-b9fc-e403014730a2";
BLEService dataService(deviceServiceUUID);
BLEStringCharacteristic dataPacketChar(deviceServicePacketCharUUID, BLERead | BLENotify, sizeof(dataToSend) + 5);

String structToString(RF_Packet &data){ // converts RF packet struct into a deconstructable string format for BLE
  String result = String(data.power) + "/";
  result += String(data.rotate) + "/";
  result += String(data.driveX) + "/";
  result += String(data.driveY) + "/";
  result += String(data.driveW) + "/";
  return result;
}

void setup() {
  Serial.begin(9600);

  // set device and local name for BLE advertising
  BLE.setDeviceName("KiwiGlove");
  BLE.setLocalName("KiwiGlove");
  
  // Initialize BLE
  if (!BLE.begin()) {
    Serial.println("Starting BLE failed!");
    while (1);
  }
  BLE.setAdvertisedService(dataService);
  dataService.addCharacteristic(dataPacketChar);
  BLE.addService(dataService);
  String dataBytes = structToString(dataToSend);
  dataPacketChar.setValue(dataBytes);
  BLE.advertise();

  // set LED pins
  pinMode(redPin, OUTPUT);
  pinMode(greenPin, OUTPUT);
  pinMode(bluePin, OUTPUT);
  pinMode(powerPin, OUTPUT);
  digitalWrite(powerPin,HIGH);

  //set Load Pulser Gate pins
  pinMode(pulse_gate,OUTPUT);
  digitalWrite(pulse_gate,gateState);
  
  // set Button Interrupt pins
  pinMode(power_button, INPUT_PULLUP);
  attachInterrupt(digitalPinToInterrupt(power_button), handlePowerPress, FALLING); // only when pin drops to gnd
  pinMode(rotate_button, INPUT_PULLUP);
  attachInterrupt(digitalPinToInterrupt(rotate_button), handleRotatePress, FALLING);

  // intializing radio
  radio.begin();
  radio.openWritingPipe(address);
  radio.setPALevel(RF24_PA_HIGH); // set power level for expected broadcast range
  radio.setChannel(100); // set RF channel to avoid common WiFi channels (0-99)
  radio.stopListening();  // Set module as transmitter

  // initialize IMU (Accel, Gyro and Mag)
  IMU.begin();

  while(!(IMU.accelerationAvailable() && IMU.gyroscopeAvailable() && IMU.magneticFieldAvailable())); // wait until sensors are ready
  // read in and initialize Home position starting values
  IMU.readAcceleration(ax,ay,az);
  IMU.readGyroscope(gx,gy,gz);
  IMU.readMagneticField(mx, my, mz);

  prev_time = millis();
  // calibrateGyroscope();

  // Magnetometer Calibration
  float mx_offset = (mx_max + mx_min) / 2.0;
  float my_offset = (my_max + my_min) / 2.0;
  float mz_offset = (mz_max + mz_min) / 2.0;

  float mx_scale = (mx_max - mx_min) / 2.0;
  float my_scale = (my_max - my_min) / 2.0;
  float mz_scale = (mz_max - mz_min) / 2.0;

  mx = (mx - mx_offset) / mx_scale;
  my = (my - my_offset) / my_scale;
  mz = (mz - mz_offset) / mz_scale;

  // Compute roll & pitch from accelerometer
  float roll  = atan2(ay, az) * 180.0 / PI;
  float pitch = atan2(-ax, sqrt(ay * ay + az * az)) * 180.0 / PI;

  // Compute tilt-compensated yaw from magnetometer
  float Xh = mx * cos(pitch * PI / 180.0) + mz * sin(pitch * PI / 180.0);
  float Yh = mx * sin(roll * PI / 180.0) * sin(pitch * PI / 180.0) + my * cos(roll * PI / 180.0) - mz * sin(roll * PI / 180.0) * cos(pitch * PI / 180.0);
  float yaw_mag = atan2(Yh, Xh) * 180.0 / PI;

  // Normalize yaw_mag to 0-360 degrees
  // if (yaw_mag < 0) yaw_mag += 360.0;
  // if (yaw_mag > 360) yaw_mag -= 360.0;
  roll_g = roll;
  pitch_g = pitch;
  yaw_g = yaw_mag;
  comp_yaw_g = yaw_mag;

  base_roll = roll;
  base_pitch = pitch;
  base_yaw = yaw_mag;
}

void loop() {
  
  // set LED based on state of Buttons
  if (power_buttonPressed) curColour = rotate_buttonPressed ? Yellow : Green;
  else curColour = Red;
  set_ledColour(curColour);

  // Load Pulser circuit check (swaps between 1 and 30 seconds)
  unsigned long pulse_curTime = millis();
  if (pulse_curTime - pulse_prevTime >= interval){
    pulse_prevTime = pulse_curTime;
    gateState = gateState ? LOW : HIGH;
    digitalWrite(pulse_gate,gateState);
    interval = gateState ? pulse_ON : pulse_OFF;
  }

  // if calibrate flag is set by buttons, then we update Home tilt position
  if (calibrate_flag){
    // Magnetometer Calibration
    float mx_offset = (mx_max + mx_min) / 2.0;
    float my_offset = (my_max + my_min) / 2.0;
    float mz_offset = (mz_max + mz_min) / 2.0;

    float mx_scale = (mx_max - mx_min) / 2.0;
    float my_scale = (my_max - my_min) / 2.0;
    float mz_scale = (mz_max - mz_min) / 2.0;

    mx = (mx - mx_offset) / mx_scale;
    my = (my - my_offset) / my_scale;
    mz = (mz - mz_offset) / mz_scale;

    // Compute roll & pitch from accelerometer
    float roll  = atan2(ay, az) * 180.0 / PI;
    float pitch = atan2(-ax, sqrt(ay * ay + az * az)) * 180.0 / PI;

    // Compute tilt-compensated yaw from magnetometer
    float Xh = mx * cos(pitch * PI / 180.0) + mz * sin(pitch * PI / 180.0);
    float Yh = mx * sin(roll * PI / 180.0) * sin(pitch * PI / 180.0) + my * cos(roll * PI / 180.0) - mz * sin(roll * PI / 180.0) * cos(pitch * PI / 180.0);
    float yaw_mag = atan2(Yh, Xh) * 180.0 / PI;

    // Normalize yaw_mag to 0-360 degrees
    // if (yaw_mag < 0) yaw_mag += 360.0;
    // if (yaw_mag > 360) yaw_mag -= 360.0;
    roll_g = roll;
    pitch_g = pitch;
    yaw_g = yaw_mag;
    comp_yaw_g = yaw_mag;

    base_roll = roll;
    base_pitch = pitch;
    base_yaw = yaw_mag;

    calibrate_flag = false;
  }

  // when all sensors are available, calculate current PRY values and get difference with Home PRY values
  // use difference to calcuate desired drive vector values
  if (IMU.accelerationAvailable() && IMU.gyroscopeAvailable() && IMU.magneticFieldAvailable()) {
    IMU.readAcceleration(ax, ay, az);
    IMU.readGyroscope(gx, gy, gz);
    IMU.readMagneticField(mx, my, mz);

    // apply Gyro offsets
    gx -= gx_offset;
    gy -= gy_offset;
    gz -= gz_offset;

    // calculate dt
    now_time = millis();
    dt = (now_time - prev_time) / 1000.0;
    prev_time = now_time;

    // calculate independent Gyro Yaw Prediction to be used with Kalman_Mag prediction later
    comp_yaw_g += gz * dt;

    // Apply Magnetometer Calibration
    float mx_offset = (mx_max + mx_min) / 2.0;
    float my_offset = (my_max + my_min) / 2.0;
    float mz_offset = (mz_max + mz_min) / 2.0;

    float mx_scale = (mx_max - mx_min) / 2.0;
    float my_scale = (my_max - my_min) / 2.0;
    float mz_scale = (mz_max - mz_min) / 2.0;

    mx = (mx - mx_offset) / mx_scale;
    my = (my - my_offset) / my_scale;
    mz = (mz - mz_offset) / mz_scale;

    // Compute roll & pitch from accelerometer
    float roll_a  = atan2(ay, az) * 180.0 / PI;
    float pitch_a = atan2(-ax, sqrt(ay * ay + az * az)) * 180.0 / PI;
    
    // Compute final Roll and Pitch with Accel predictions and Gyro values in Kalman Filter
    float pitch = kalmanPitch.getAngle(pitch_a, gx, dt);
    float roll = kalmanRoll.getAngle(roll_a, gy, dt);

    // Compute tilt-compensated yaw from magnetometer
    float Xh = mx * cos(pitch * PI / 180.0) + mz * sin(pitch * PI / 180.0);
    float Yh = mx * sin(roll * PI / 180.0) * sin(pitch * PI / 180.0) + my * cos(roll * PI / 180.0) - mz * sin(roll * PI / 180.0) * cos(pitch * PI / 180.0);
    float yaw_mag = atan2(Yh, Xh) * 180.0 / PI;

    // Compute Kalman yaw with Mag prediction and Gyro values in Kalman Filter
    float kalman_yaw = kalmanYaw.getAngle(yaw_mag, gz, dt);
    // Combine Kalman yaw with Gyro yaw prediction (much more reliable) to get final yaw
    float yaw = 0.98 * (comp_yaw_g) + (1 - 0.98) * kalman_yaw;
    
    // Compute difference between Home and Current PRY values
    diff_roll = roll - base_roll;
    diff_pitch = pitch - base_pitch;
    diff_yaw = yaw - base_yaw;

    // Update drive vector in RF packet based on PRY values between -45 and 45 degrees of range mapped to -1 to 1 in the user's frame of reference
    dataToSend.driveW = ((constrain(abs(diff_yaw),0,45) - 0.0) * (1.0 - 0) / (45.0 - 0) + 0) * (diff_yaw > 0 ? -1 : 1);
    dataToSend.driveX = ((constrain(abs(diff_pitch),0,45) - 0.0) * (1.0 - 0) / (45.0 - 0) + 0) * (diff_pitch > 0 ? -1 : 1);
    dataToSend.driveY = ((constrain(abs(diff_roll),0,45) - 0.0) * (1.0 - 0) / (45.0 - 0) + 0) * (diff_roll > 0 ? 1 : -1);     
  }
  // Update button states in RF packet
  dataToSend.power = power_buttonPressed;
  dataToSend.rotate = rotate_buttonPressed;
  
  bool success = radio.write(&dataToSend, sizeof(dataToSend)); // send data over RF to Robot

  // check for BLE connections to arduino device
  BLEDevice central = BLE.central();
  BLE.poll();
  if(central){ // if connection conver RF packet to a string and update advertised information on BLE service
    String dataBytes = structToString(dataToSend);
    dataPacketChar.writeValue(dataBytes); // BLE service will automatically notify connected device of an update (flag set: BLENotify)
  }

  delay(10); // artificially introduced delay, otherwise Robot nRF24 module serial buffer would get overflow  
}

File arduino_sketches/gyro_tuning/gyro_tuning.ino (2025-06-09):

#include <Arduino_BMI270_BMM150.h>
#include <MadgwickAHRS.h>

Madgwick filter;
const float sample_rate = 100;
const float gyro_scale = 1; // use to increase responsiveness of filter to chanegs
                            // if too large, values will become unstable

float ax, ay, az;  // Accelerometer

float gx_offset = 0.00, gy_offset = 0.05, gz_offset = -0.24; // intended for calibration at high gyro_scale to help mitigate value drift
const int num_samples = 5000;


float gx = 0, gy = 0, gz = 0;  // Gyroscope
float measure_gx, measure_gy, measure_gz;
float pitch_g = 0.0, roll_g = 0.0, yaw_g = 0.0;

float mx, my, mz;  // Magnetometer
float mx_min =  -99.0, my_min =  -47.0, mz_min =  -46.0;
float mx_max = 27.0, my_max = 89.0, mz_max = 100.0;
bool calibrating = false;  // Set to false after collecting enough data

float base_roll = 0; // Anchor base values for tilt comparisons
float base_pitch = 0;
float base_yaw = 0;

float diff_roll = 0;
float diff_pitch = 0;
float diff_yaw = 0;

float now_time, prev_time, dt;

void calibrateGyroscope() {
  float gx_sum = 0.0, gy_sum = 0.0, gz_sum = 0.0;

  for (int i = 0; i < num_samples; i++) {
    while (!IMU.gyroscopeAvailable());

    IMU.readGyroscope(gx, gy, gz);

    gx *= gyro_scale;
    gy *= gyro_scale;
    gz *= gyro_scale;

    // Accumulate the readings
    gx_sum += gx;
    gy_sum += gy;
    gz_sum += gz;

    delay(5); // Small delay to allow consistent sampling
  }

  // Calculate the average offset for each axis
  gx_offset = gx_sum / num_samples;
  gy_offset = gy_sum / num_samples;
  gz_offset = gz_sum / num_samples;
  Serial.print(gx_offset);
  Serial.print(" | ");
  Serial.print(gy_offset);
  Serial.print(" | ");
  Serial.println(gz_offset);
}

void setup() {
  // put your setup code here, to run once:
  Serial.begin(9600);
  while(!Serial);

  IMU.begin();
  // prints out sample rate of Accel and Gyro sensors
  Serial.println("NEW SET: ");
  Serial.print(IMU.accelerationSampleRate());
  Serial.println(" Hz");
  Serial.print(IMU.gyroscopeSampleRate());
  Serial.println(" Hz");

  // get intitial Home tilt PRY values
  while(!(IMU.accelerationAvailable() && IMU.gyroscopeAvailable() && IMU.magneticFieldAvailable()));
  IMU.readAcceleration(ax,ay,az);
  IMU.readGyroscope(gx,gy,gz);
  IMU.readMagneticField(mx, my, mz);

  filter.begin(sample_rate);

  prev_time = millis();
  
  // RUN THIS FUNCTION HERE TO GET GYROSCOPE CALIBRATION VALUES
  // calibrateGyroscope(); 

  // Magnetometer Calibration
  float mx_offset = (mx_max + mx_min) / 2.0;
  float my_offset = (my_max + my_min) / 2.0;
  float mz_offset = (mz_max + mz_min) / 2.0;

  float mx_scale = (mx_max - mx_min) / 2.0;
  float my_scale = (my_max - my_min) / 2.0;
  float mz_scale = (mz_max - mz_min) / 2.0;

  mx = (mx - mx_offset) / mx_scale;
  my = (my - my_offset) / my_scale;
  mz = (mz - mz_offset) / mz_scale;

  // Compute roll & pitch from accelerometer
  float roll  = atan2(ay, az) * 180.0 / PI;
  float pitch = atan2(-ax, sqrt(ay * ay + az * az)) * 180.0 / PI;

  // Compute tilt-compensated yaw from magnetometer
  float Xh = mx * cos(pitch * PI / 180.0) + mz * sin(pitch * PI / 180.0);
  float Yh = mx * sin(roll * PI / 180.0) * sin(pitch * PI / 180.0) + my * cos(roll * PI / 180.0) - mz * sin(roll * PI / 180.0) * cos(pitch * PI / 180.0);
  float yaw_mag = atan2(Yh, Xh) * 180.0 / PI;

  // Normalize yaw_mag to 0-360 degrees
  if (yaw_mag < 0) yaw_mag += 360.0;
  if (yaw_mag > 360) yaw_mag -= 360.0;
  yaw_g = yaw_mag;

  base_roll = roll;
  base_pitch = pitch;
  base_yaw = yaw_mag;

}
// calibrating functions
void calibrating_MagSensor(){ 
  if (IMU.magneticFieldAvailable()) {
    IMU.readMagneticField(mx, my, mz);

    if (calibrating) { // use when calibrating flag is set to true to get limit values
      // Record min and max values
      if (mx < mx_min) mx_min = mx; if (mx > mx_max) mx_max = mx;
      if (my < my_min) my_min = my; if (my > my_max) my_max = my;
      if (mz < mz_min) mz_min = mz; if (mz > mz_max) mz_max = mz;

      Serial.print("Calibrating... Min: "); Serial.print(mx_min); Serial.print(", ");
      Serial.print(my_min); Serial.print(", "); Serial.println(mz_min);
      
      Serial.print("Max: "); Serial.print(mx_max); Serial.print(", ");
      Serial.print(my_max); Serial.print(", "); Serial.println(mz_max);
    } 
    else { // test calibration results when flag is set to false
        // Compute calibration offsets and scaling factors
        float mx_offset = (mx_max + mx_min) / 2.0;
        float my_offset = (my_max + my_min) / 2.0;
        float mz_offset = (mz_max + mz_min) / 2.0;

        float mx_scale = (mx_max - mx_min) / 2.0;
        float my_scale = (my_max - my_min) / 2.0;
        float mz_scale = (mz_max - mz_min) / 2.0;

        // Apply calibration
        mx = (mx - mx_offset) / mx_scale;
        my = (my - my_offset) / my_scale;
        mz = (mz - mz_offset) / mz_scale;

        // Compute roll, pitch, yaw
        float roll  = atan2(my, mz) * 180.0 / PI;
        float pitch = atan2(-mx, sqrt(my * my + mz * mz)) * 180.0 / PI;
        float yaw   = atan2(my, mx) * 180.0 / PI;

        // Normalize yaw to 0-360 degrees
        if (yaw < 0) yaw += 360.0;

        Serial.print("Roll: "); Serial.print(roll);
        Serial.print(" Pitch: "); Serial.print(pitch);
        Serial.print(" Yaw: "); Serial.println(yaw);
    }
  }
}

// see results functions
void results_AccelOnly(){
  if(IMU.accelerationAvailable()){ // results are -4 to 4 in G's - gravity
    IMU.readAcceleration(ax, ay, az);
    float pitch = atan2(ax, sqrt( pow(ay, 2) + pow(az, 2))) * 180 / M_PI;
    float roll = atan2(ay, sqrt( pow(ax, 2) + pow(az, 2))) * 180 / M_PI;
    
    Serial.print("Accel: ");
    Serial.print(pitch);
    Serial.print(" | ");
    Serial.println(roll);
  } // gives us pretty stable roll and pitch values
}
void results_GyroOnly(){
  if(IMU.gyroscopeAvailable()){ // results are 0 to 2000 in degress/sec
    IMU.readGyroscope(gx, gy, gz);

    gx -= gx_offset;
    gy -= gy_offset;
    gz -= gz_offset;

    now_time = millis();
    dt = (now_time - prev_time) / 1000.0;
    prev_time = now_time;

    pitch_g += gy * dt;
    roll_g += gx * dt;
    yaw_g += gz * dt;
    Serial.print("Gyro: ");
    Serial.print(pitch_g);
    Serial.print(" | ");
    Serial.print(roll_g);
    Serial.print(" | ");
    Serial.println(yaw_g);
  } // hard to maintain home position difference of 0
}
void results_MagOnly(){
  if(IMU.magneticFieldAvailable()){ // results are 0 to 2000 in degress/sec
    IMU.readMagneticField(mx, my, mz);

    float roll = atan2(my, mz) * 180.0 / PI;
    float pitch = atan2(-mx, sqrt(my * my + mz * mz)) * 180.0 / PI;
    float yaw = atan2(my, mx) * 180.0 / PI;

    if (yaw < 0) yaw += 360.0;
    Serial.print("Mag: ");
    Serial.print(pitch);
    Serial.print(" | ");
    Serial.print(roll);
    Serial.print(" | ");
    Serial.println(yaw);
  } // results are very unstable and heavily subject to environmental conditions
}
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

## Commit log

2025-06-09 Add files via upload
    Adding arduino files
2025-06-09 Add files via upload
    Adding CAD files
    [G2_Battery_Case.step, G2_Battery_Hook.step, G2_Battery_WireHook.step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]
